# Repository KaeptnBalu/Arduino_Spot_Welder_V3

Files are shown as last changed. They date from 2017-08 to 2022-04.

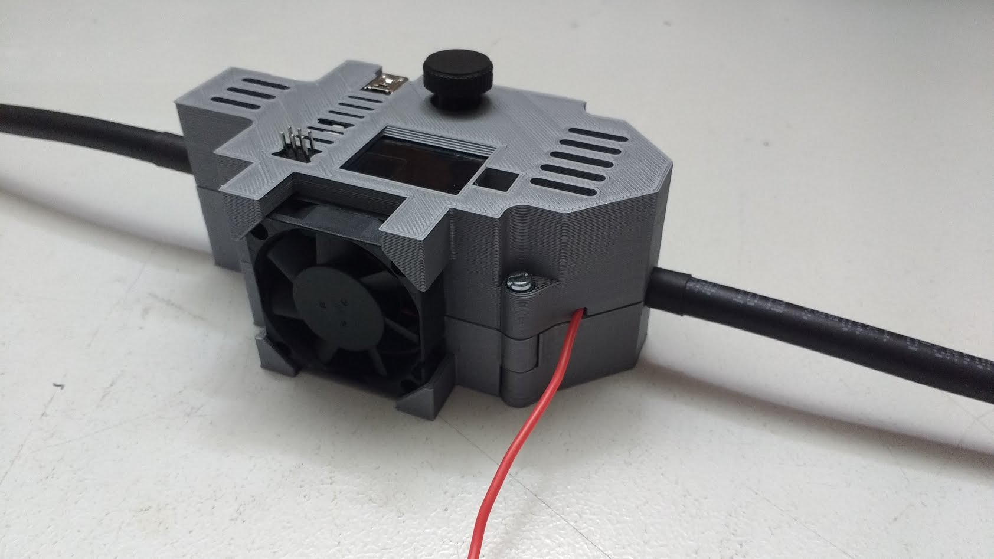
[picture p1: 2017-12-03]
Parts/Spot Welder V3 Case/SWV3_case_v2_assembly_11.jpg

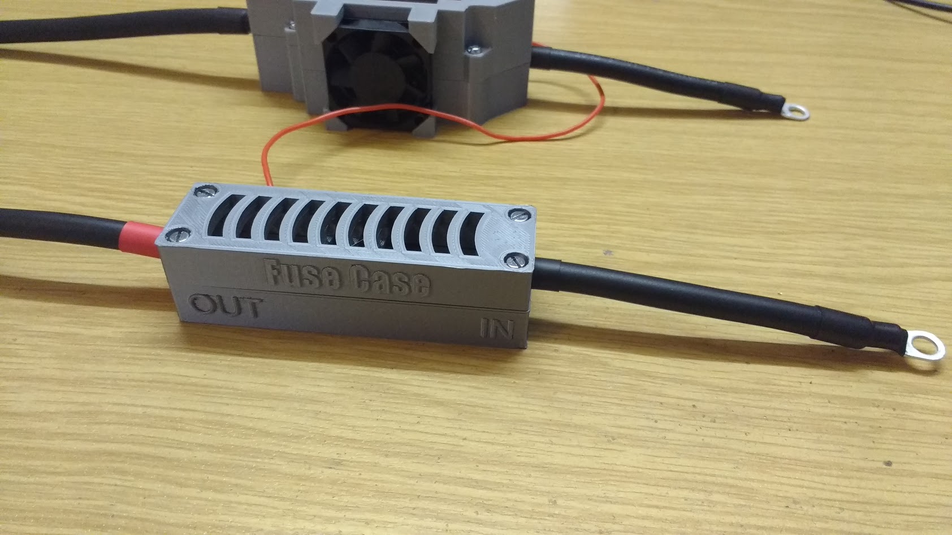
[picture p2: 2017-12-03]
Parts/Spot Welder V3 Case/Fuse_Case_assembly_14.jpg

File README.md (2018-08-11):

# Arduino_Spot_Welder_V3

This is the latest V3 of the Arduino Spot Welder. The previous V2 can be found here https://github.com/KaeptnBalu/Arduino_Spot_Welder_V2

An Arduino based Spot Welder for battery welding 
- Build Guide: http://www.instructables.com/id/DIY-Arduino-Battery-Spot-Welder/
- Introduction Video: https://www.youtube.com/watch?v=CNmvx2JSCvA
- Project Homepage: https://malectrics.eu/

Improvements in V3:

- Mosfet PCB now with 2oz copper layer and wider traces which connect the high current carrying mosfet legs to the u-shaped aluminum part
- “AutoPulse” feature, which automatically activates a pulse after a defined delay time when both welding tips touch the nickel strip (thanks to Petr Zverina for the idea)
- 7 segment display replaced by OLED display
- potentiometer replaced by rotary encoder
- Menu system to easy adjust the low battery alarm, AutoPulse delay and short pulse time
- powered directly by car battery, no more need for extra power supply
- TVS diode integrated on the mosfet pcb, no external diodes necessary
- upgraded Mosfets to IRFB7430 (they can handle up to 1000A welding current with no problem)
- Standby feature: after 5 minutes of inactivity the Spot Welder will go to standby and the foot switch and AutoPulse will be deactivated while in standby.
- u-shaped aluminum parts is now riveted to the pcb

This Spot Welder can be used to weld 18650 batteries. It uses a 12V car battery as welding current supply. Typically one 40Ah 440A battery delivers enough current to get good welds with 0.15mm nickel strips and even 0.25mm nickel strips. For thicker nickel strips maybe you will need bigger battery or two in paralell.

The Welder generates a double pulse, where the first one is 12% of the time of the second one by default. Pulse time of the main pulse is adjustable by the rotary encoder and displayed on the screen in ms so you can exactly adjust the time. Its adjustable from 1 … 100 mS by default. (adjustable up to 500ms in the system menu)

If you want to download the project click on "clone or download" on this page. Downloading single files sometimes seems to cause some files to be corrupted while downloading.

You can get parts to build your own Spot Welder or prebuilt kits at https://malectrics.eu/

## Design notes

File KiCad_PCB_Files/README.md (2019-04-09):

These are the pcb files for the Spot welder V3

V3.3
- The mosfet board was updated with following improvements: 
- Much wider traces on the bottom of the pcb for the high current connection to the u-shaped aluminum part
- Mosfet gate resistors directly on the mosfet board, very close to the mosfet gate pins
- All 8 Pins of the female 8 pin header that connects the Arduino and mosfet board are now connected to each other, which eliminates contact problems.
- compatible to all Spot Welder Arduino Boards V3 or later

V3.2
- the Arduino Board was updated so it is now possible to mount a 3.5mm terminal block to the input pads. 
- the voltage measurement now connects directly to the 12V input pad instead of behind the schottky diode in the previous version. This guarantuees a more precise voltage measurement.
- the 8 small SMAJ13A-13-F TVS diodes have been removed from the mosfet board. There is now one of these diodes on the Arduino board that protects all mosfet gates at once.

V3.1

There is a new V3.1 of the mosfet board available. It is fully compatible with the Arduino Board V3, so you only need to upgrade the mosfet board if you already built a V3 Spot Welder. 

Improvements:

    4 TVS diodes instead of only 1

This improvement makes it more capable of higher CCA rated car batteries. In my tests it handled a 800 CCA car battery for a few hundred welds in a row without problems. But using this powerfull batteries operates the welder near its maximum limits so the recommended car battery size is still 400...600 CCA

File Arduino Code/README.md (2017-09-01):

This is the Arduino Code for the Spot Welder V3. 
Do not use it with the older V2 pcbs. It is not compatible with these.

You need to have the Ardafruit_GFX library and the Ardafruit_SSD1306 library installed in your Arduino IDE to sucessfully compile the Code.

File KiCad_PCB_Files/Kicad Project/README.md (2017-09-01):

These are the KICAD project files for the Arduino Spot Welder V3

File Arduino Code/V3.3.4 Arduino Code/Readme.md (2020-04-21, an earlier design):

This is V3.3.4 of the Arduino Code

Improvements:

- fix weld counter, it can now count up to 65535
- add over volatge warning when input voltage is 14.5 V or higher

When upgrading from an earlier V3 version of the Arduino Code to this one you need to perform a full reset of the welder in the system menu after the update.

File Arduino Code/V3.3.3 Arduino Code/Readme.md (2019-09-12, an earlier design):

This is V3.3.3 of the Arduino Code

Improvements:

- fix slow progress bar drawing problem

You can also apply this fix to older versions of the Arduino Code. All you have to do is change this line of code in the drawProgress function:

        res = ++o->step > steps;

to these two lines:

        o->step = (int)(millis()-o->millis)/(o->time/steps);
        res = o->step > steps;

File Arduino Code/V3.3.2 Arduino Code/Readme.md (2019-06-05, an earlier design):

This is V3.3.2 of the Arduino Code

Improvements:
- Weld time can be set down to 1ms (before minimum was 3ms)
- Short Pulse (preheat pulse) percentage can be adjusted down to 0% (0% turns the short pulse off)
- on weld times below 3ms the short pulse (preheat pulse) will be automatically disabled
- battery voltage only updates about every 15 seconds now
- low battery message can be canceled by clicking the rotary encoder
- code is now compatible with the newer Adafruit SSD1306 and GFX library versions

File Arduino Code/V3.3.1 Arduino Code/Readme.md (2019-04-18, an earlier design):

Improvements in V3.3.1
- The Welder will now recognize if the foot switch is wired wrong and display an error message.

Description:
The foot switch needs to be used in no configuration, if it is connected in nc configuration (which means contacts closed when the switch is not pushed) an error message will be displayed during the start up of the spot welder.

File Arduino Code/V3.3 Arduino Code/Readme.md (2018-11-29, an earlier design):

Changes in V3.3

The Auto Pulse feature was improved. 
Many thanks to the Spot Welder user Arturs Jelohovskis for implementing this feature into the Arduino code.

What it does:
- added indication of probes shortcut on the screen
- added indication of delay BEFORE welding as progress bar (if probes are disconnecting during wait then AutoPulse stops)
- added indication of delay AFTER the welding pulse as progress bar.

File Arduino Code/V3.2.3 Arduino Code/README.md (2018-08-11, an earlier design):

Changes in V3.2.3

Bugfix: 
The weld counter does now automatically reset to 0 as soon as it reaches 9999 welds.
This was done because the display failed when the weld counter reached 10.000 welds, due to problems with variable types.

In case you dont want to update your software to the latest version:
In the older software versions you can solve the display problem by doing a "Full Reset" in the system menu. 
This will reset the weld counter to 0. Then you can do 9999 welds before the problem occurs again.

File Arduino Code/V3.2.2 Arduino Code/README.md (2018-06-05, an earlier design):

Changes in V3.2.2:

The software reset function has been removed because there were many complains that it is to complicated to update the Arduino Nano Bootloder. 
This change eliminates the need to install the SoftwareReset library and you also dont need to change the default bootloader of the Arduino Nano to the OptiBoot Bootloader anymore.

How does this change the Spot Welder usability ?

When you are in the sytem menu and click on the reboot, the safe reset or the full reset button you need to power of the Spot Welder manually to perform a reset.

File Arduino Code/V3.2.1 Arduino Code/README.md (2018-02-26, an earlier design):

This is version 3.2.1 of the Arduino Code.

New features:
The Version 3.2.1 Update introduces a weld pulse measurement feature.
This feature allows the Spot Welder to measure the voltage drop across the two welding cables and the Spot Welder itself. 
From that value it then calculates the Amps.

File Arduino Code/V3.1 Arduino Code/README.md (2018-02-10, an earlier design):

This is the new completely redesigned V3.1 Arduino Code for the Arduino Spot Welder.

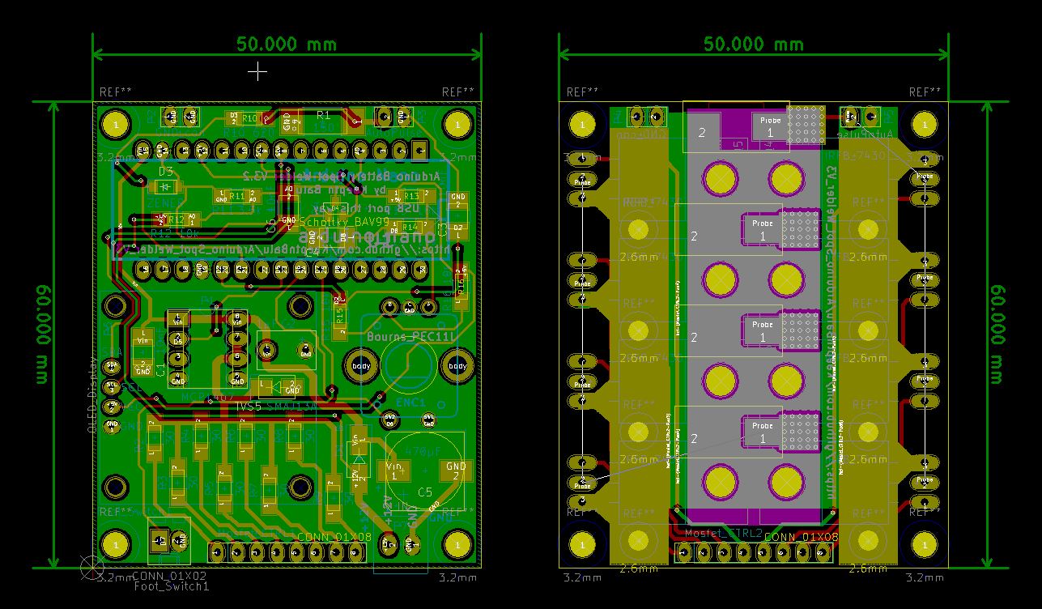
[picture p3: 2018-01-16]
KiCad_PCB_Files/Spot_Welder_V3.2_PCB_Layout.JPG

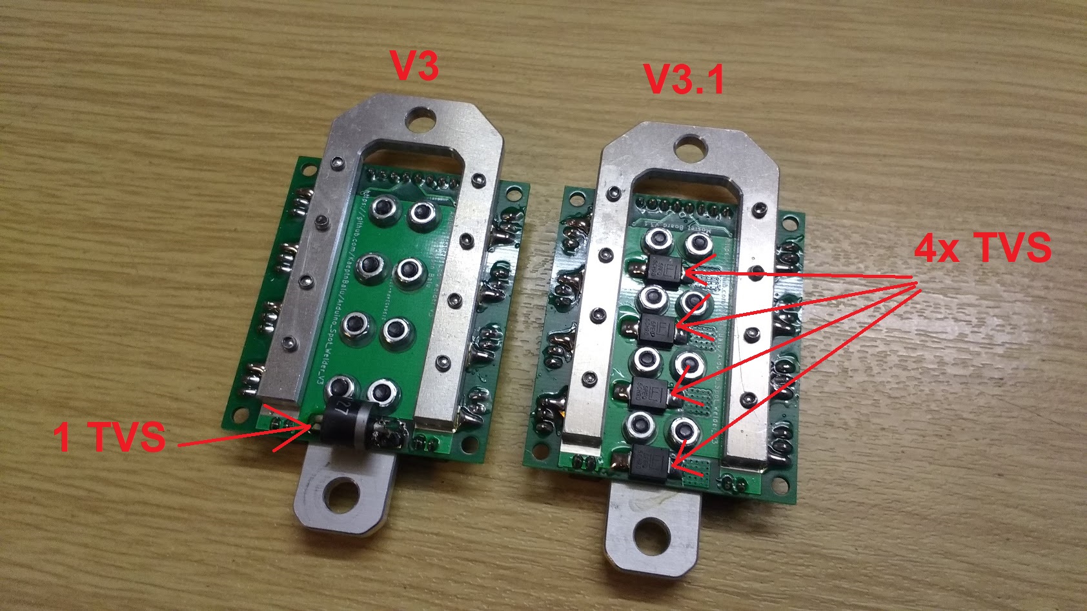
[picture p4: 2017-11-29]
KiCad_PCB_Files/mosfet_pcb_V3_vs_V3.1.jpg

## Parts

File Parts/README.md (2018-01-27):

<b>For a complete parts list take a look at the BOM file</b>

These are the parts you need to buy for building the Spot Welder V3. With the Mouser.com Shop Link you can directly ad all electronic component parts to your shopping cart. 

Not included in the Mouser shopping cart:
- 1x Arduino Nano
- 1x OLED Display

Parts I bought at the local hardware store:

- 1x piece of 16x70mm aluminium about 3 or 4mm thick
- Some 16mm² cable and short piece of thick solid copper wire for the probes tips

You can get ready made welding cables, aluminum parts and pcb sets at www.malectrics.eu if you dont want to make them yourself.

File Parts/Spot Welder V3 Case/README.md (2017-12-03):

This is a 3d printable case for the Arduino Spot Welder V3.

The files are available to download from thingiverse:

https://www.thingiverse.com/thing:2600227

https://www.thingiverse.com/thing:2615364

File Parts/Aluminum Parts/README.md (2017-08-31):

Use the PDF template to cut the aluminum pieces from 4mm material.

The u-shaped piece is optional. You can either solder the thick wire bend to an u-shape directly to the pcb as before or cut this aluminum piece and screw it with m2 screws to the pcb.

You can also take a look at the 3d and dxf drawings to manufacture the aluminum parts with a cnc or something else.

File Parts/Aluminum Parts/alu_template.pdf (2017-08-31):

# Cut from 3 - 4 mm thick aluminum

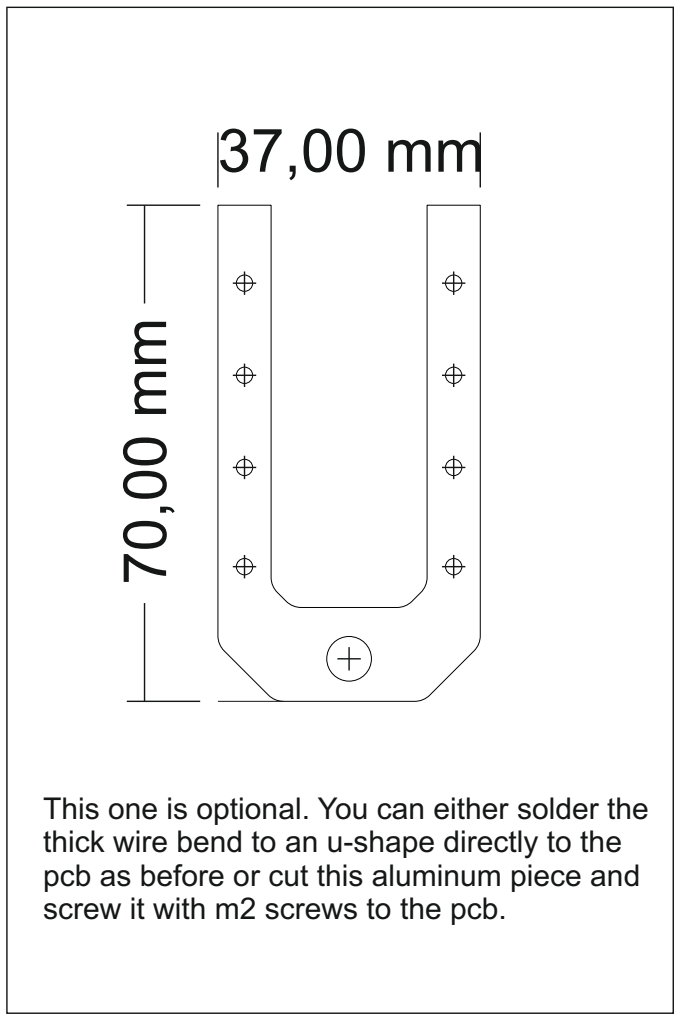
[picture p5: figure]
screw it with m2 screws to the pcb.

This one is optional. You can either solder the thick wire bend to an u-shape directly to the pcb as before or cut this aluminum piece and

70,00 mm

17,00 mm

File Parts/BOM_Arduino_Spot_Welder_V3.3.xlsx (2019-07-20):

 |  | Mouser.com Parts |  | Complete Shopping Card Link (https://www.mouser.com/ProjectManager/ProjectDetail.aspx?AccessID=131d2ccc2d)
Quantity | PCB Reference | Name | Mouser.com Part Number | Price/piece | Price all | Note
8 | IRFB_7430 | Mosfet IRFB 7430 40V 409A | 942-IRFB7430PBF (http://www.mouser.de/Search/ProductDetail.aspx) | 2.76 € | 22.08 €
1 | P1 MCP1407 | Mosfet Driver MCP1407-E/P | 579-MCP1407-E/P (http://www.mouser.de/Search/ProductDetail.aspx) |  | 0.90 €
1 | Bourns_PEC11L | Rotary Encoder | 652-PEC11L4220FS0015 (http://www.mouser.de/Search/ProductDetail.aspx) |  | 1.70 €
2 | Arduino Nano | 1x15 Pol Female Pin Header | 992-15FX1-254MM (http://www.mouser.de/Search/ProductDetail.aspx) | 1.06 | 2.12 €
1 | Mosfet_CTRL2 | 1x8pol female header | 437-8018700810001101 (http://www.mouser.de/Search/ProductDetail.aspx) | 0.66 € | 0.81 €
2 | P4,P5 | 1x2pol female header | 437-8018700210001101 (http://www.mouser.de/Search/ProductDetail.aspx) | 0.221 | 0.44 €
1 | OLED_Display | 1x4pol female header | 517-974-01-04-RK (http://www.mouser.de/Search/ProductDetail.aspx) |  | 0.62 €
1 | Mosfet_CTRL1, P2, P3 | 1x16 Pol Male Pin Header | 538-22-28-4160 (http://www.mouser.de/Search/ProductDetail.aspx) |  | 0.66 €
1 | Foot_Switch | PCB connector 2pin | 710-61900211121 (http://www.mouser.de/Search/ProductDetail.aspx) |  | 0.48 €
1 | P7 | Terminal Block | 710-691214110002 (https://www.mouser.de/ProductDetail/710-691214110002) |  | 0.75 €
1 | P1 MCP1407 | IC socket 8 pole | 571-1-2199298-2 (http://www.mouser.de/Search/ProductDetail.aspx) |  | 0.09 €
1 | D1 | SMD-Schottky 60V 1A | 750-CDBA160-G (http://www.mouser.de/Search/ProductDetail.aspx?R=CDBA160-Gvirtualkey59960000virtualkey750-CDBA160-G) |  | 0.34 €
1 | Zener D3 | SMD Zener diode 4,3V 0,5W | 78-MMSZ4687-E3-08 (http://www.mouser.de/Search/ProductDetail.aspx) |  | 0.17 €
1 | D4 | Schottky BAV99 | 863-BAV99LT1G (http://www.mouser.de/Search/ProductDetail.aspx?R=BAV99LT1Gvirtualkey58410000virtualkey863-BAV99LT1G) |  | 0.10 €
4 | TVS | TVS Diode 14,4V 5kW | 576-5.0SMDJ13A (https://www.mouser.de/ProductDetail/576-5.0SMDJ13A) | 1.69 € | 6.76 €
1 | TVS5 | TVS Diode 13V 400W | 621-SMAJ13A-13-F (http://www.mouser.de/Search/ProductDetail.aspx) |  | 0.32 €
1 | C2 | film capacitor 1 µF RM5 | 505-MKS2C041001FMSSD (http://www.mouser.de/Search/ProductDetail.aspx) |  | 0.26 €
4 | C1, C3, C4, C6 | ceramic capacitor 0,01µF SMD | 581-12103D103MAT2A (http://www.mouser.de/Search/ProductDetail.aspx) | 0.17 € | 0.51 €
1 | C5 | electrolytic capacitor 470µF 25V | 647-UWT1E471MNL1S (http://www.mouser.de/Search/ProductDetail.aspx) |  | 0.52 €
1 | R1 | Resistor 1206 SMD 1 kOhm | 603-AC1206FR-071KL (https://www.mouser.de/ProductDetail/Yageo/AC1206FR-071KL?qs=sGAEpiMZZMu61qfTUdNhG19HzxXL1i6itFKVZ7nWm2k%3D) |  | 0.10 €
10 | R2, R3, R4, R5, R6, R7, R8, R9 | Resistor 1206 SMD 30 Ohm | 603-RC1206FR-0730RL (http://www.mouser.de/Search/ProductDetail.aspx) | 0.02 | 0.20 €
10 | R17,R18,R19,R20,R21,R22,R23,R24 | Resistor 1206 SMD 30 Ohm | 603-RC1206FR-0730RL (http://www.mouser.de/Search/ProductDetail.aspx) | 0.02 | 0.20 € | optional to make the Arduino Board compatible with mosfet boards older than V3.3. If you only use V3.3 mosfet boards you can bridge the pads instead of populating resistors.
10 | R10 | Resistor 1206 SMD 620 Ohm | 603-RC1206FR-07620RL (http://www.mouser.de/Search/ProductDetail.aspx) | 0.02 € | 0.20 €
10 | R11 | Resistor 1206 SMD 3,3 kOhm | 603-RC1206FR-073K3L (http://www.mouser.de/Search/ProductDetail.aspx) | 0.02 € | 0.20 €
10 | R12 … R16 | Resistor 1206 SMD 10 kOhm | 603-RC1206FR-0710KL (http://www.mouser.de/Search/ProductDetail.aspx) | 0.02 € | 0.20 €
 |  |  | Components Total: |  | 40.73 €
 |  |  | incl. 19%tax |  | 48.47 €
 |  |  | Other Parts
Quantity |  | Name | Description | Price/piece | Price all | Link / Where to buy
1 |  | Arduino Nano |  |  | 2.15 € | https://www.banggood.com/ATmega328P-Nano-V3-Controller-Board-Compatible-Arduino-p-940937.html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
1 |  | OLED Diplay 0,96" 128x64 | take care of correct pinout (GND - VCC - SCL - SDA) |  | 4.73 € | https://www.banggood.com/0_96-Inch-12864-OLED-Module-4-Pin-IC-I2C-IIC-Communication-p-1219948.html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
1 |  | Alu 17x70x4mm + 37x70x4mm | see alu_template.pdf (https://github.com/KaeptnBalu/Arduino_Spot_Welder_V2/blob/master/Parts/Aluminum_Parts/alu_template.pdf) |  | 2 € | local hardware Store or https://malectrics.eu/
8 |  | M3x10 screw + nuts | for mosfets assembly |  | 0.50 € | local hardware store
8 |  | M3 Nylon Washers | for mosfets assembly |  | 0.50 € | local hardware store
8 |  | M2.5x8 screws + nuts | for u-alu ssembly |  | 0.50 € | local hardware store
1 |  | 1m 16 mm² flexible cable | for welding cable |  | 3 € | e.g. old car starter cable or https://www.schweisshelden.de/schweisskabel-h01n2-d-16-mm2-48129
1 |  | 0,1m 16mm² solid copper wire | for the welding tips |  | 1 € | local hardware store
2 |  | cable lug for 16 mm² | for welding cable | 0.6 | 1.20 € | local hardware store or http://www.voelkner.de/products/9287/Ringkabelschuh-16-25mm-6mm-Gelb.html
1 |  | Luster Terminal 16mm² | welding tip connection |  | 2.00 € | local hardware store
1 |  | battery terminals | for car battery |  | 2.95 € | local hardware store or https://malectrics.eu/
1 |  | PCB Set | Arduino + Mosfet PCB |  | 5.95 € | https://malectrics.eu/
2 |  | nylon spacers M2 x 12mm + M2x5 screws for OLED display | OPTIONAL |  | 3.00 € | Ebay or Aliexpress
1 |  | Foot Switch | OPTIONAL |  | 5.95 € | https://malectrics.eu/
1 |  | 300A Fuse | OPTIONAL |  | 2.95 € | https://malectrics.eu/
 |  |  | Other Parts Total: |  | 38.38 €
 |  |  | TOTAL COST |  | 86.85 € | (with Optonal Parts)
 |  |  |  |  | 74.95 € | (without OPTIONAL Parts)

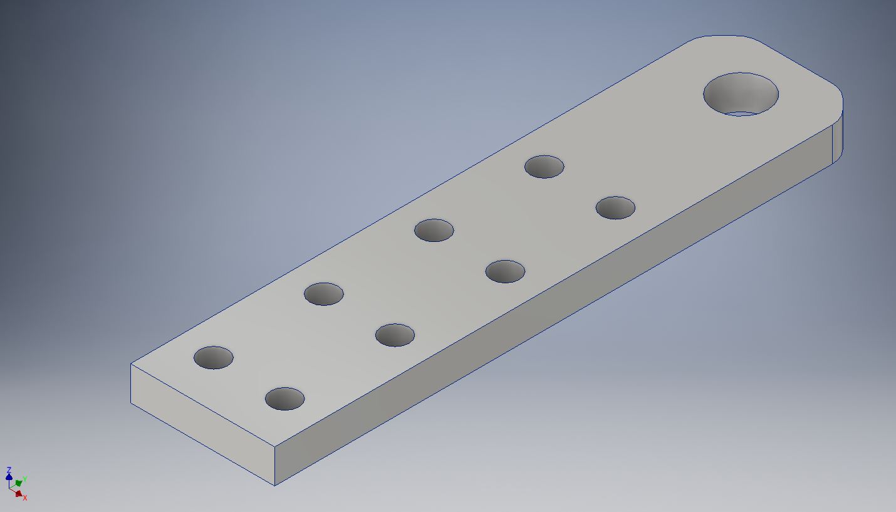
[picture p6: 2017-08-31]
Parts/Aluminum Parts/Part2_new.JPG

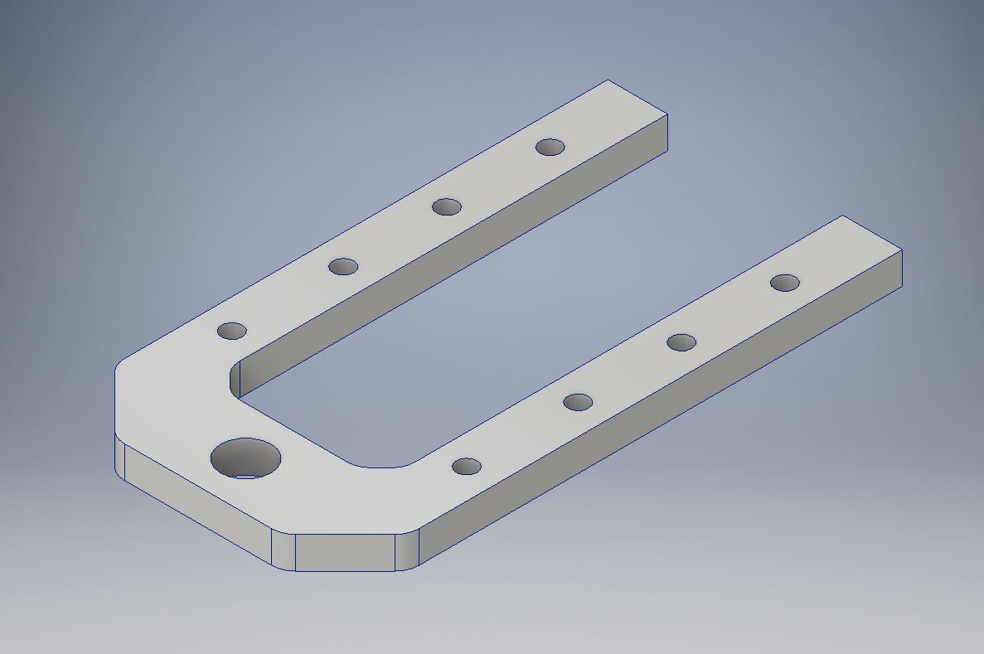
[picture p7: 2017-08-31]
Parts/Aluminum Parts/Part1_new.JPG

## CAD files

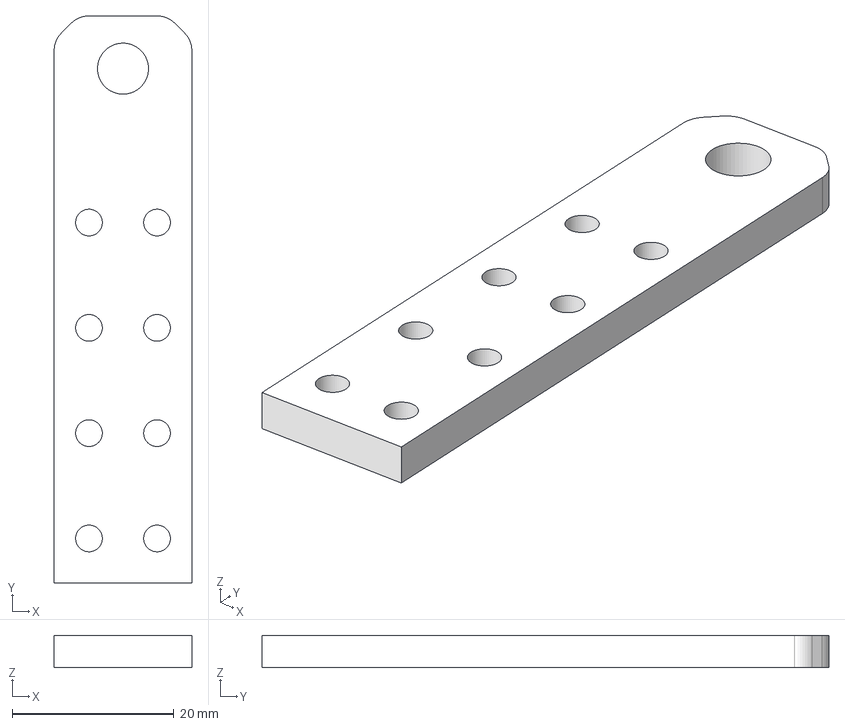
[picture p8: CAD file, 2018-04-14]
Parts/Aluminum Parts/Part2_new.stp
17.0 x 70.0 x 4.00 mm

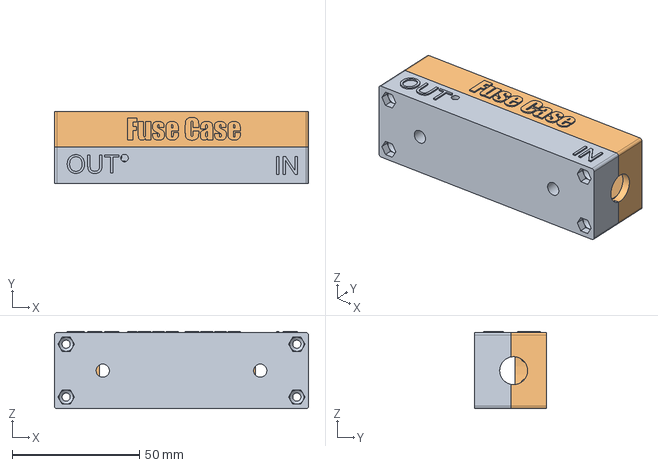
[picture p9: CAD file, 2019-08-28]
Parts/Spot Welder V3 Case/CAD Files/ANL_Fuse_Case.step
100.0 x 28.5 x 30.5 mm

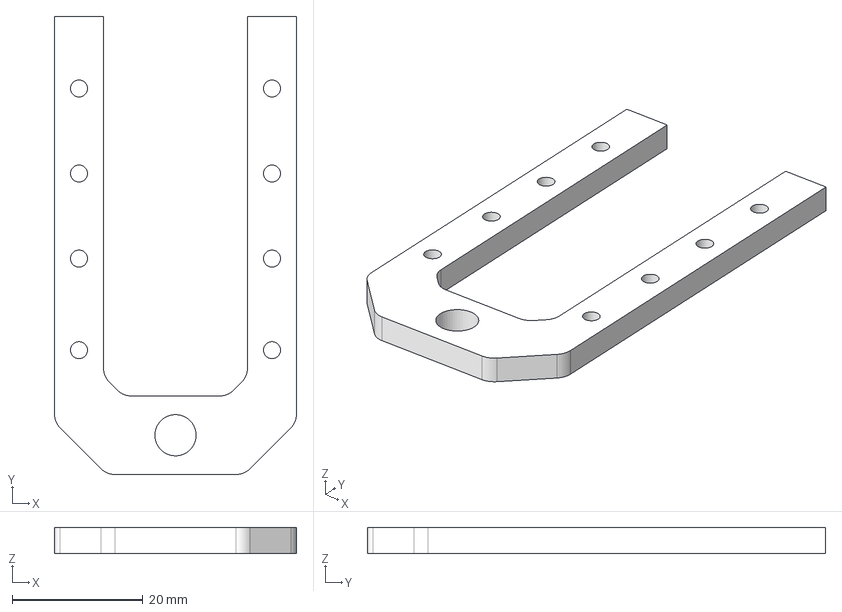
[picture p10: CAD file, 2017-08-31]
Parts/Aluminum Parts/Part1_new.stp
37.0 x 70.0 x 4.00 mm

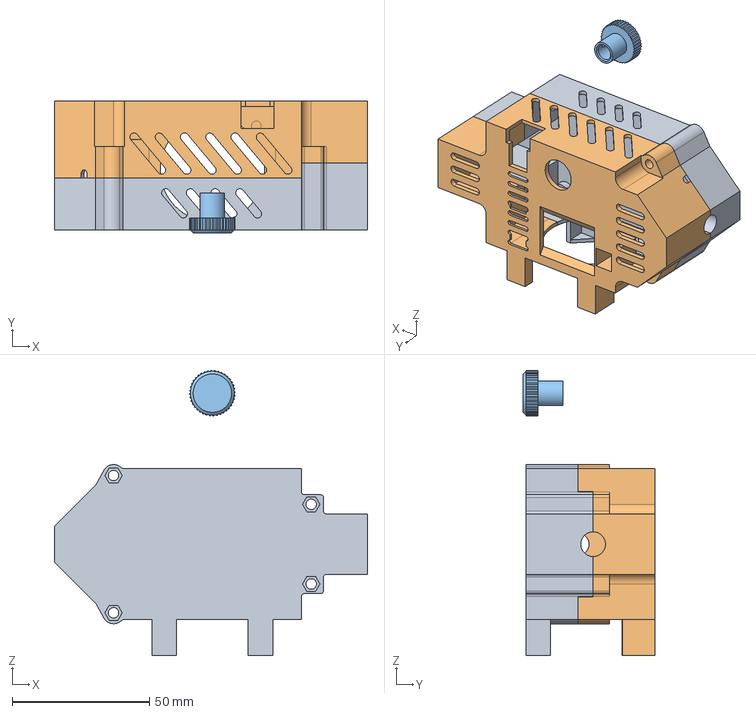
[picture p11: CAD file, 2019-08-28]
Parts/Spot Welder V3 Case/CAD Files/Case_Spot Welder_V3.step
114.0 x 48.0 x 103.9 mm

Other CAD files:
Parts/Aluminum Parts/Part1_new.dwg
Parts/Aluminum Parts/Part1_new.dxf
Parts/Aluminum Parts/Part1_new.ipt
Parts/Aluminum Parts/Part2_new.dwg
Parts/Aluminum Parts/Part2_new.dxf
Parts/Aluminum Parts/Part2_new.ipt
Parts/Spot Welder V3 Case/CAD Files/ANL_Fuse_Case.f3d
Parts/Spot Welder V3 Case/CAD Files/Case_Car_Bat_Mount_Spot Welder_V3.f3d
Parts/Spot Welder V3 Case/CAD Files/Case_Spot Welder_V3.f3d

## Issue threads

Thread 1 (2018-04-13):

Add Part2_new.stp

PaoloElMarinelo, 2018-04-13:
Hi !
First I want to say thank you for all you make in this project, it's the best spot welder I know !
Please could you add the .STP file from Part2_new in Arduino_Spot_Welder_V3/Parts/Aluminum Parts/ ?
Thank you very much.
Paolo

KaeptnBalu, 2018-04-14:
Hi,
Thanks for pointing out the missing file. I added it.

Closed 2018-04-14.

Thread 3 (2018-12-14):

V3.2.3: deprecated OLED constructor makes pin 4 unusable

crteensy, 2018-12-14:
I designed a custom top PCB with an arduino pro mini, and used pin 4 for one of the encoder inputs. That didn't work out of the box, because pin 4 appeared to be stuck high. It's not used in the schematic and also not defined in the header block with pin numbers. This was hard to track down, but:

The constructor used for the OLED display is deprecated (as per adafruit's documentation). It uses a reset pin, and the reset pin is defined as pin 4 in the OLED part of the spot welder header file (you don't have the bare source file in the repo so I can't link to it).

The correct constructor to use is (line
`Adafruit_SSD1306 display(128, 64, &Wire);       /**< OLED display object */`

And the reset pin definition can be removed:
//#define OLED_RESET          4               /**< OLED mode */

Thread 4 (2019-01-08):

Slow screen refresh rate

ignasurba, 2019-01-08:
With the latest [Adafruit_SSD1306](https://github.com/adafruit/Adafruit_SSD1306/releases/tag/1.2.9) library the I2C clock is ~32kHz, due to wireClk in the library being 0.

The following will fix the issue.
`Adafruit_SSD1306 display(OLED_RESET);       /**< OLED display object */`
change to:
`Adafruit_SSD1306 display(128, 64, &Wire, OLED_RESET, 800000L); /**< OLED display object */`

Good luck!

bseishen, 2019-04-15:
+1 on this. Redraw times at slow data rate is causing auto pulse to be nowhere accurate. 2sec is more like 10 seconds.

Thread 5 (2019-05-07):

mosfet board state led (new idea)

dreamstruct, 2019-05-07:
HI KaeptnBalu

I have an idea

About add state led to mosfet borad

Is it possible to connect the 10k resistor to the

 MCP1407 output pin and then connect the LED to GND?
This can quickly get the output state of the mosfet board

Does this cause mosfet to crash?

Please evaluate his possibilities

Thank you very much.

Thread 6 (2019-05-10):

KICAD R1 resistor in version 3.3 should be modified to 1Kom ?

dreamstruct, 2019-05-10:
I see in other version is for 150 ohm resistor SMD 3521 2w
However, version 3.3 was changed to 1206 1kom
Is this a bug?

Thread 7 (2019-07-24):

Version 3.3

snmcma, 2019-07-24:
Version 3.3 in a working state, or is it only a temporary project? Can I order a fee from Chinese friends?

KaeptnBalu, 2019-07-24:
Version 3.3 is working fine

snmcma, 2019-08-31:
>
>
> Version 3.3 is working fine

what could be the problem? in version 3.3.2 the display does not work, in version 3.3.1 the display works fine. Where could there be a mistake?

KaeptnBalu, 2019-09-01:
V3.3.2 reqires a new library versions for the display.
(Adafruit SSD1306 V1.2.9 and Adafruit GFX V1.5.3)
For more details see https://malectrics.eu/2019/06/05/arduino-spot-welder-software-installing-tutorial-v3-3-2/

snmcma, 2019-09-01:
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

nice! thnks!

snmcma, 2019-11-03:
I used another encoder (which was at hand, I always go all the way to one side (minus) it doesn’t matter which way I turn the encoder. (there is a flaw in the library)
after assembly, my welding worked 1 time and didn’t work anymore (something went wrong). In automatic mode, should there be voltage across the contacts of the electrodes? (I think one of the mosfets struck me, it shows a voltage slightly less than the input)

snmcma, 2019-11-03:
Is it not difficult for you to take large photographs from all sides? I want to make sure the assembly is correct.

KaeptnBalu, 2019-11-03:
Hi,
Did you take a look at the assembly instructions: https://malectrics.eu/pcb-set-v3-3-assembly-instructions/
There are a lot of pictures, so you can check if you got everything correct.

Measuring the battery voltage at the welding tips is normal. If it instantly sparks when you touch the nickel, then there is a problem somewhere.

snmcma, 2019-11-03:
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
he writes the data of the current pulse, but there was no pulse on the electrodes. after each pulse, you need to click on the encoder so that I can try again to make a pulse, is this normal behavior?

snmcma, 2019-11-03:
This is not too much current I had on the pulse, mosfets could burn out? I used a powerful 160,000 microfarad capacitor in parallel with the power.

snmcma, 2020-05-17:
Can you give an answer what is the reason? It works on a small power supply, but when I connect it to a car battery, I don’t learn to weld. firmware updated to 3.3.4

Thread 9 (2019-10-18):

Display Issue

Courty40, 2019-10-18:
FYI - Had an odd problem yesterday, couldn't get the OLED display to work, tried the correct libs and scanned the i2c port (I could see the display on 0x3C).

In the end I had to do the following to get it to initialise

//Adafruit_SSD1306 display(128, 64, &Wire, OLED_RESET, 800000L); /**< OLED display object */
Adafruit_SSD1306 display(OLED_RESET);

Display is a standard Chinese OLED one with the correct pin outs, described as a "SSD1306 AA140"

If I get a min will look further but all seems to be working OK..

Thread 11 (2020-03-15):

V3.3.3 Arduino Code selectedSubMenu not assigned value correctly

richard-scott, 2020-03-15:
I've migrated your code over to using PlatformIO, and I get this error when compiling it:

> Arduino Spot Welder/src/Arduino_Spot_Welder_V3_3_3.ino:539:37: warning: statement has no effect [-Wunused-value]
>                      selectedSubMenu == 0;

It is from this section:
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

My repo is here:
https://github.com/richard-scott/Arduino_Spot_Welder_V3

richard-scott, 2020-04-01:
I've squashed the error in my repo here:
https://github.com/richard-scott/Arduino_Spot_Welder_V3
I'll create a PR.

KaeptnBalu, 2020-04-01:
Awesome Job Richard. Thank you so much for your work. This actually fixed the 10.000 welds counter bug. It can now count above 10.000 without creating an error. I will implement your fix in a new V3.3.4 of the spot welder software.

Closed 2020-04-01.

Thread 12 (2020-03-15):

V3.3.3 Arduino Code - integer implicitly truncated to unsigned type

richard-scott, 2020-03-15:
I'm getting this error when compling code:

```
Arduino_Spot_Welder_V3_3_3.ino:1076:74: warning: large integer implicitly truncated to unsigned type [-Woverflow]
     setTextProp(1, (SSD1306_LCDWIDTH-(sizeof(LS_PULSEV)-1)*CHR_W*2)/2, 16);
                                                                          ^
```
This is the section of code:
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

I've not yet got a fix for it.

richard-scott, 2020-04-01:
I've squashed the error in my repo here:
https://github.com/richard-scott/Arduino_Spot_Welder_V3
I'll create a PR.

Closed 2020-04-01.

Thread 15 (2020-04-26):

Blown legs to fets

plsommerton, 2020-04-26:
Hi. This welder v3 used for only third time today decided to blow several of the fet layer legs. Any ideas what may be causing it? Cheers.phil

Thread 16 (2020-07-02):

nothing happens when button is pressed

stefi01, 2020-07-02:
the screen works ok and the pot when turned left or right moves up and down through the milliseconds but when pressed to select or set nothing happens, am i missing something, checking the arduino sketch does not reveal any pin numbers so i am a bit lost, this is a home build and not a kit, pcb is ok and was made by jlbpcb.

KaeptnBalu, 2020-07-03:
The button of the encoder is connected to GNG and pin D6 on the Arduino Nano. When you push it Pin D6 should be pulled to GND.

stefi01, 2020-07-03:
found it, got it working, thanks :)

Closed 2020-07-03.

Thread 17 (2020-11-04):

Weld current estimate to check for propper weld

geo99918, 2020-11-04:
I saw that the weld current is estimated based on the source voltage during the weld pulse, why not use this estimation as a check for a proper weld and trigger an alarm when the current was too low, or even add a menu to set the min and max values for weld current.
E.g. with a discharged car battery 12V is present at idle but during the weld pulse the voltage drops to less than 3 volts and a good weld is not created.
A more advanced version of this would be to measure the total energy delivered to the weld but this might be for another day.

Regards,
George

KaeptnBalu, 2020-11-05:
A llittle problem with the weld current measurement is that it is not super accurate. The welder uses a fixed resistance value to calculate the current flow. It can not measure the resistance itself, just the voltage drop during the pulse. This resistance can change quite a bit depending how the welding tips are placed on the nickel and how good the contact of the wleding cables is.

I think the idea to set a weld current alarm is pretty good. For that the current measurement should be accurate enough.

To calculate the total energy during pulse and then base the pulse length on that, the current measurement needs to be more precise.  If you got an idea how the welder could do a precise resistance measurement (without complicated hardware) before a weld, that would be great. I think an option to choose between energy based welding and fixed time welding would be preatty cool.

geo99918, 2020-11-05:
Maybe the current can be measured by measuring the voltage drop across a big shunt.
if current and voltage are known during the weld event a better estimation can be done if the weld was successful or not.
Maybe the resistance can be estimated using V and I but the power source internal resistance can't be ignored in this calculation.
Regarding the alarm, a buzzer would be nice to indicate that something went wrong, usually when welding the eyes are on the weld not on the screen.

Satys27, 2025-02-05:
Ok wait for my Project release, I have improved lots of features like robotic arm will weld you just need to seat tight infront of it.

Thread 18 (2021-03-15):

v3.3.4 freeze

corbolais, 2021-03-15:
Hi,
Thanks for this project, I love it.

When doing a couple of welds, the arduino regularly freezes. Only way to continue is a reset.

Any ideas as to why it is happening or what might cause it?

It happens with standard settings and modified settings as well.

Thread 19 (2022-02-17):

CAD Files

Thegribbs, 2022-02-17:
The CAD files for the design on Thingiverse (https://www.thingiverse.com/thing:2600227/files) are designed with a cutout for the battery terminal.
Do you have a copy of the f3d file for that design?

KaeptnBalu, 2022-02-19:
The f3d file has been added

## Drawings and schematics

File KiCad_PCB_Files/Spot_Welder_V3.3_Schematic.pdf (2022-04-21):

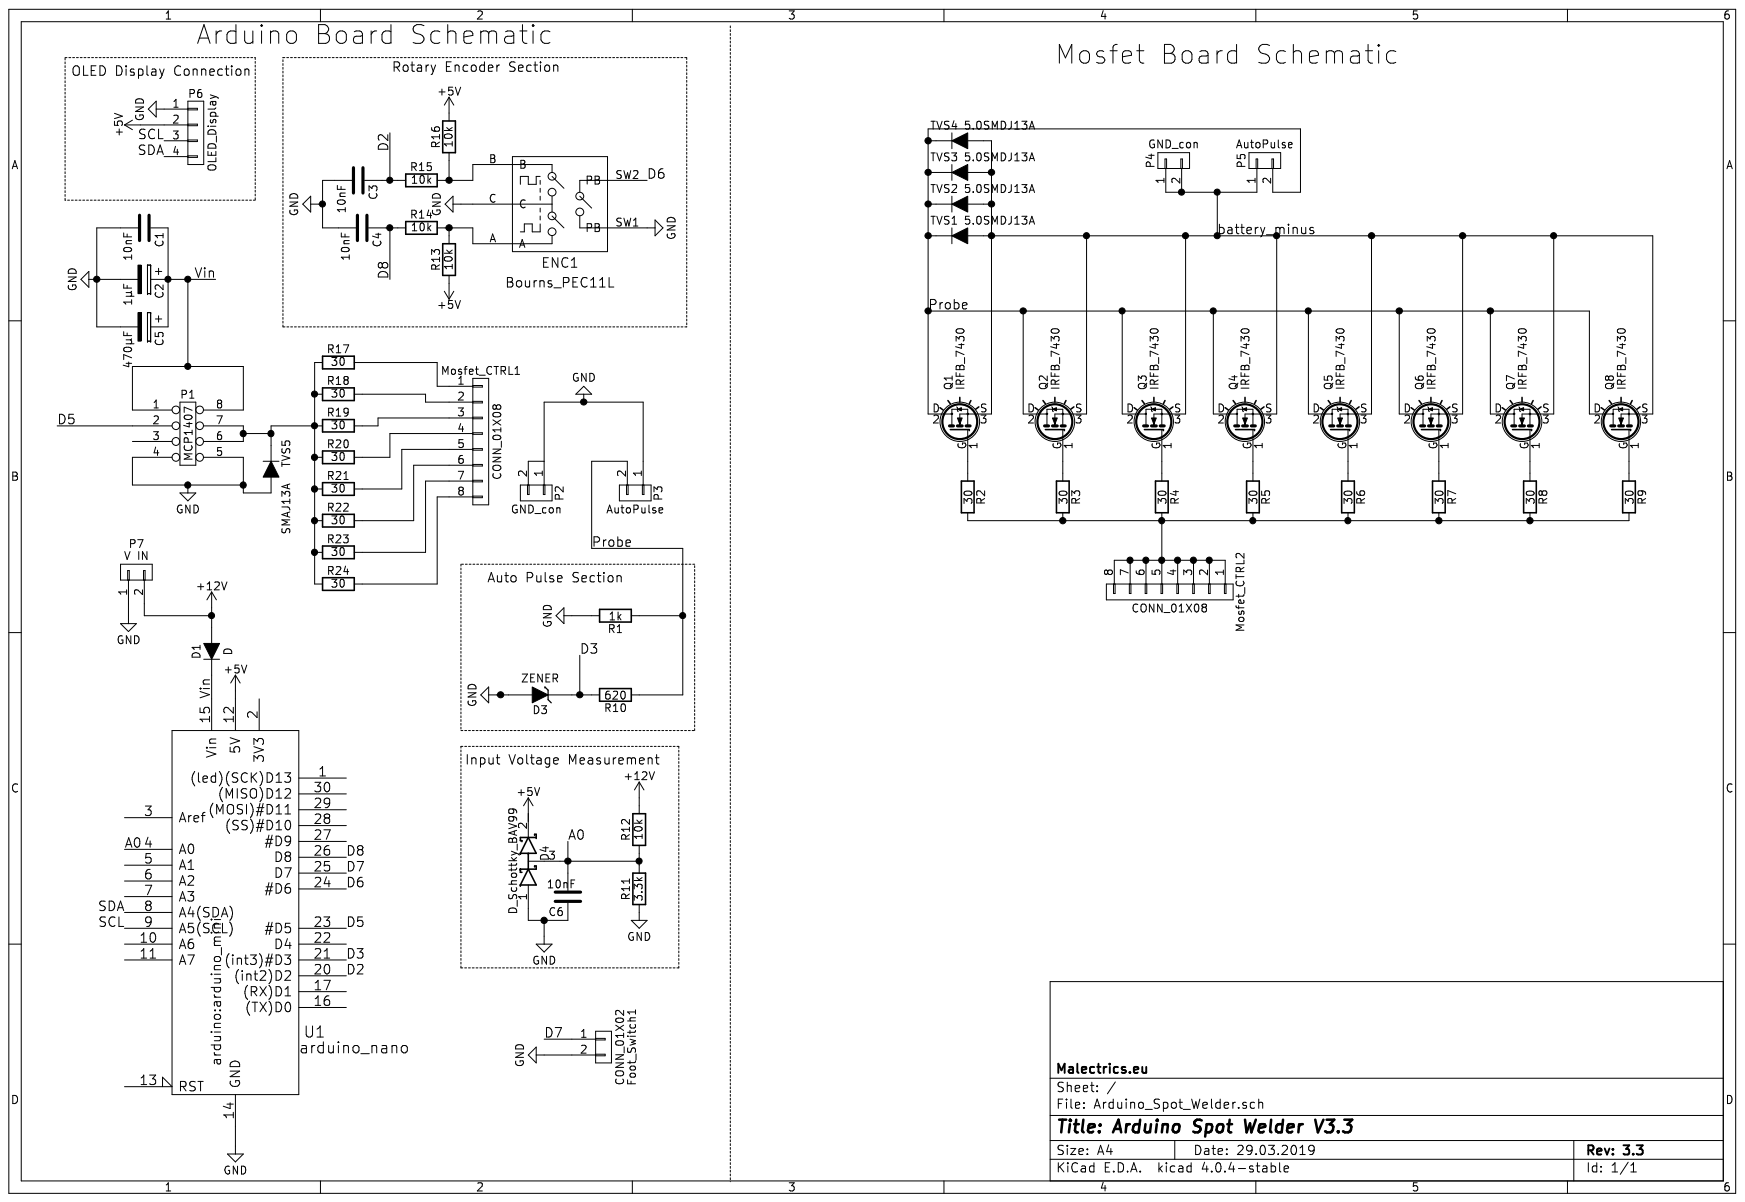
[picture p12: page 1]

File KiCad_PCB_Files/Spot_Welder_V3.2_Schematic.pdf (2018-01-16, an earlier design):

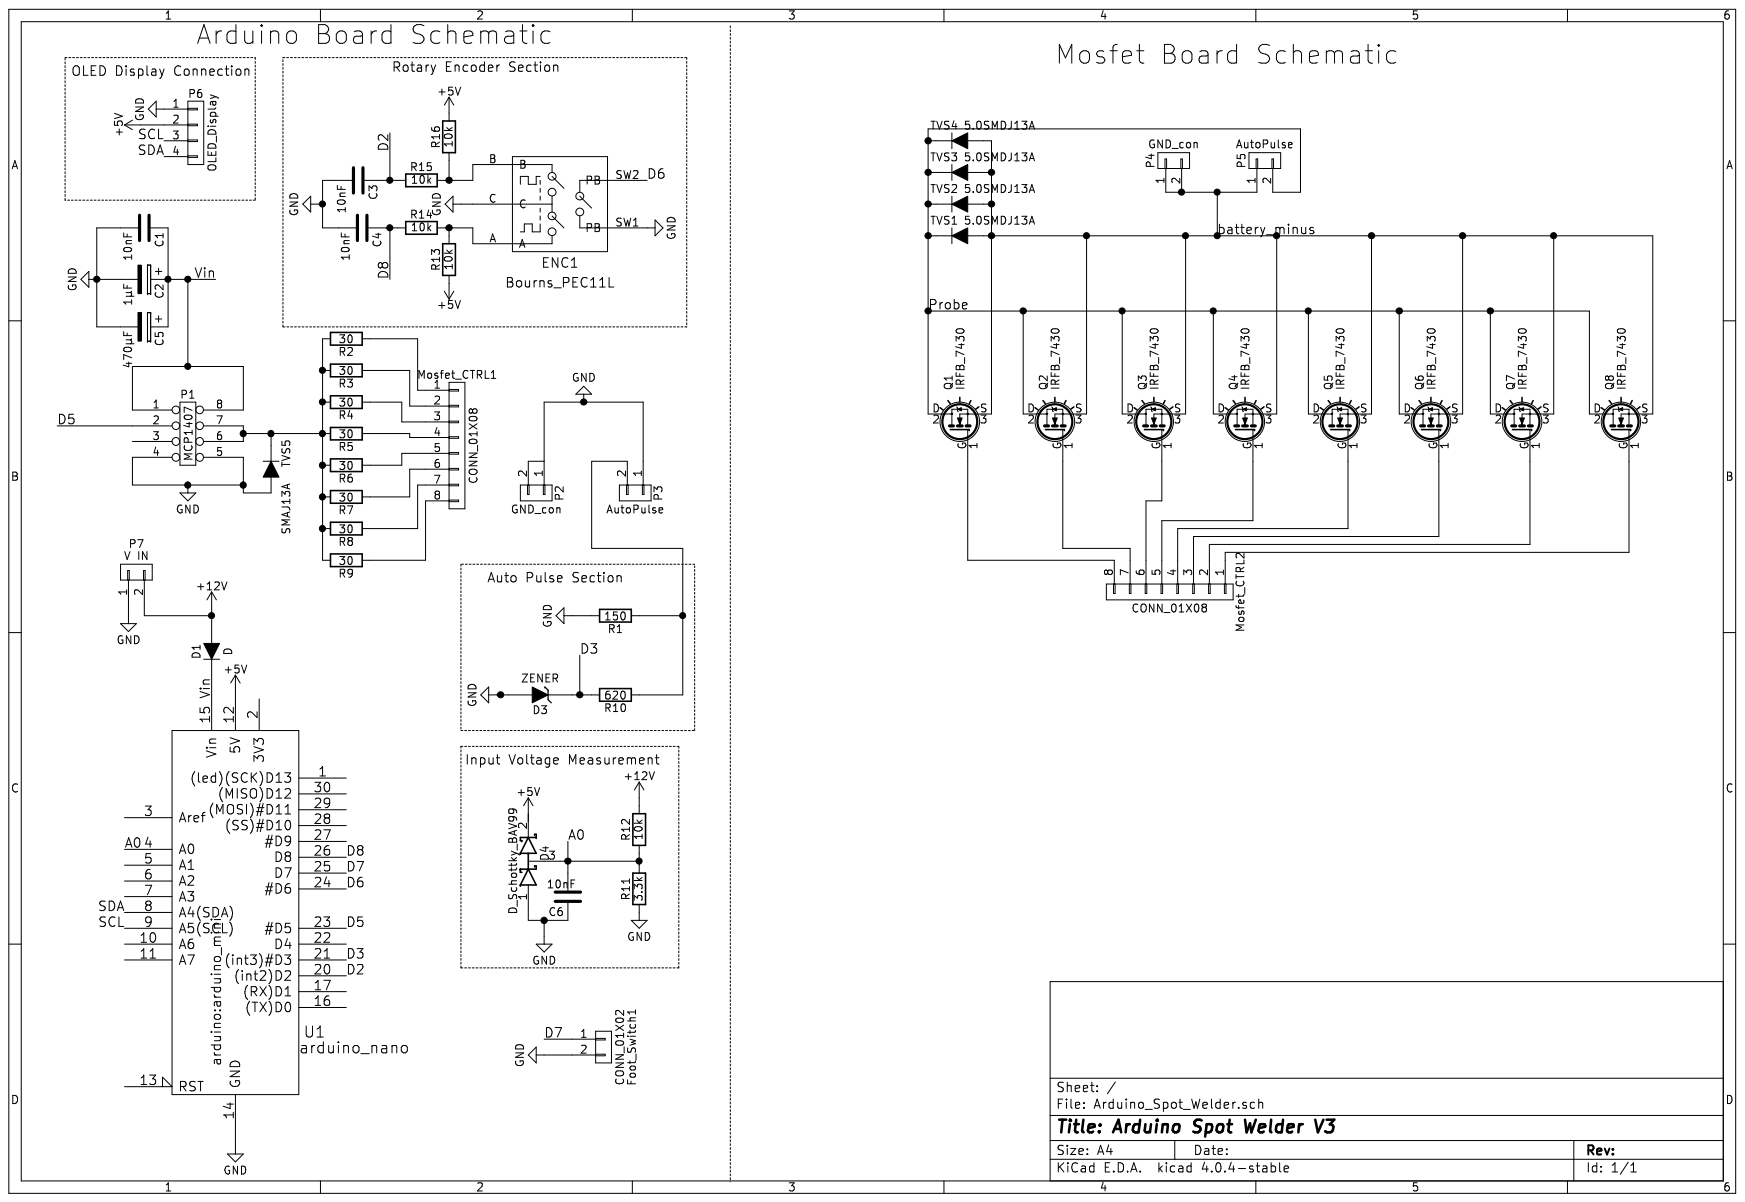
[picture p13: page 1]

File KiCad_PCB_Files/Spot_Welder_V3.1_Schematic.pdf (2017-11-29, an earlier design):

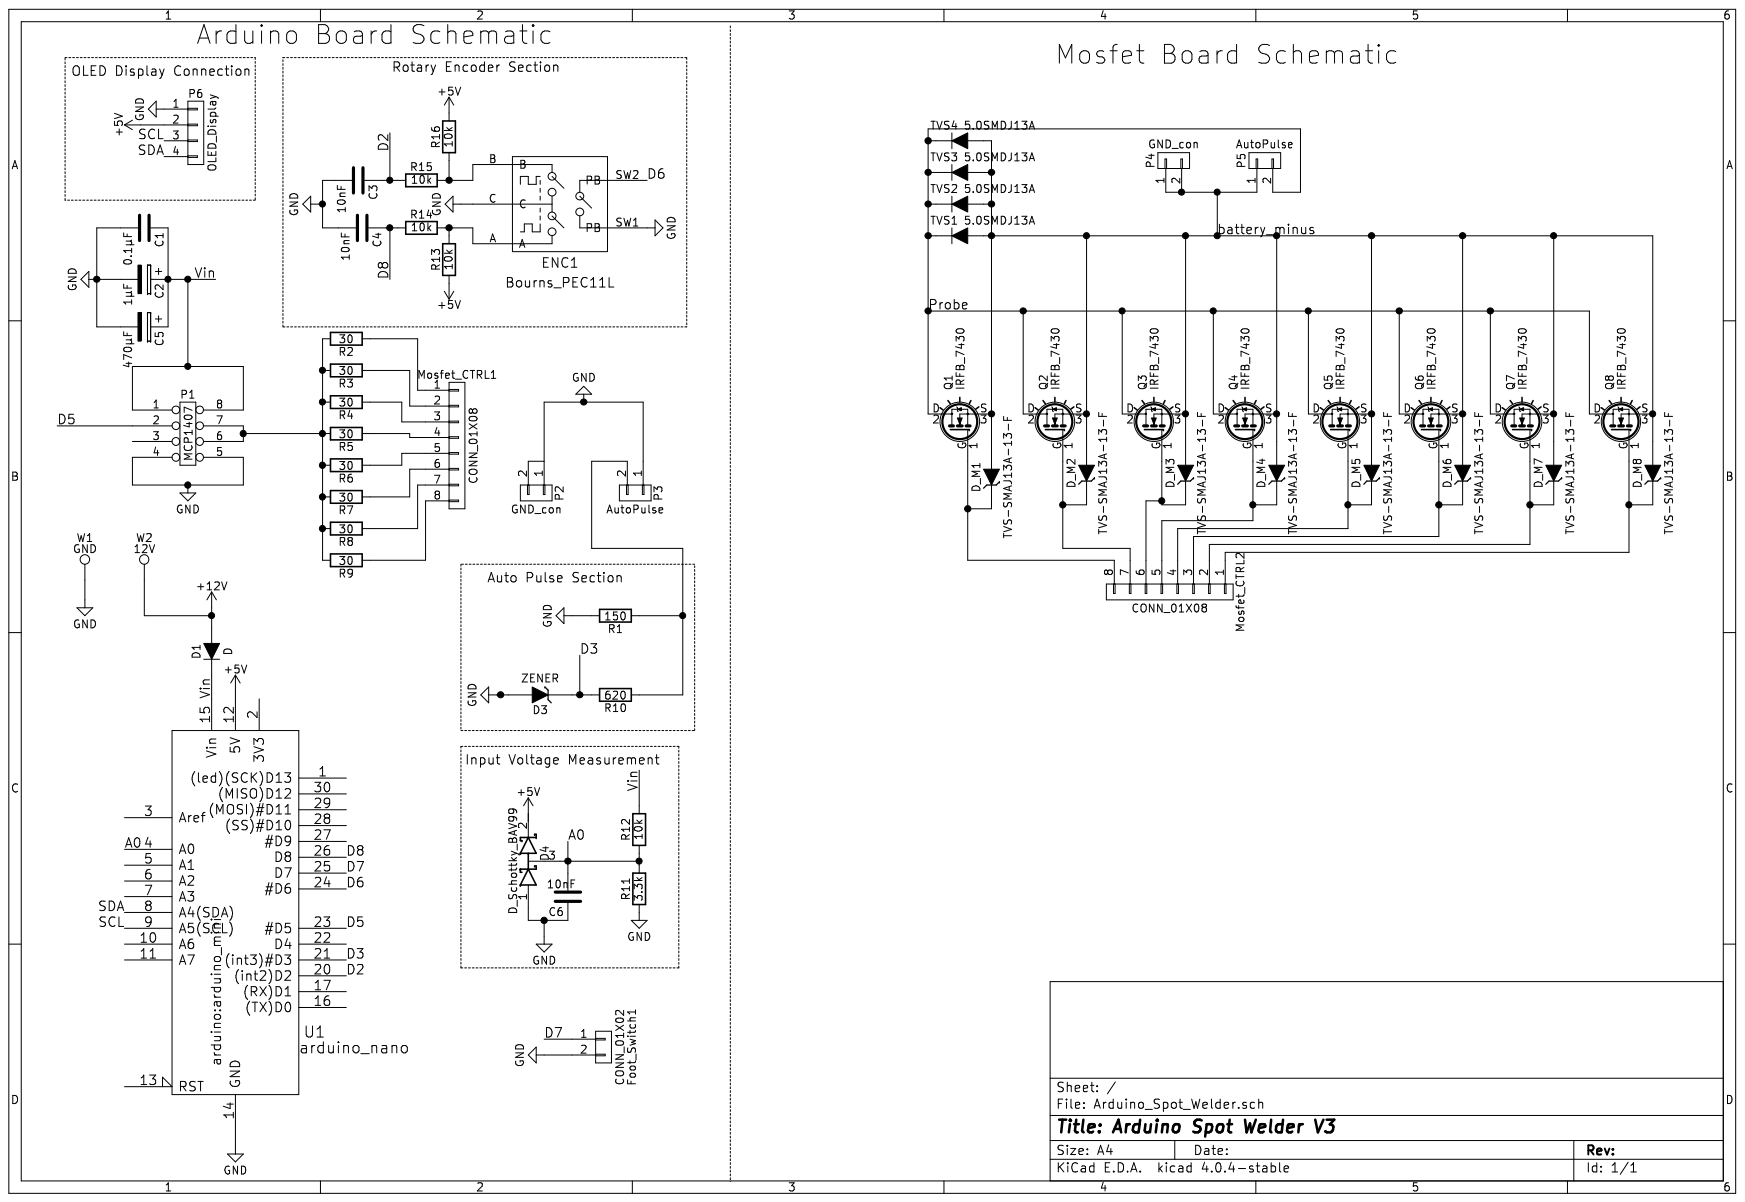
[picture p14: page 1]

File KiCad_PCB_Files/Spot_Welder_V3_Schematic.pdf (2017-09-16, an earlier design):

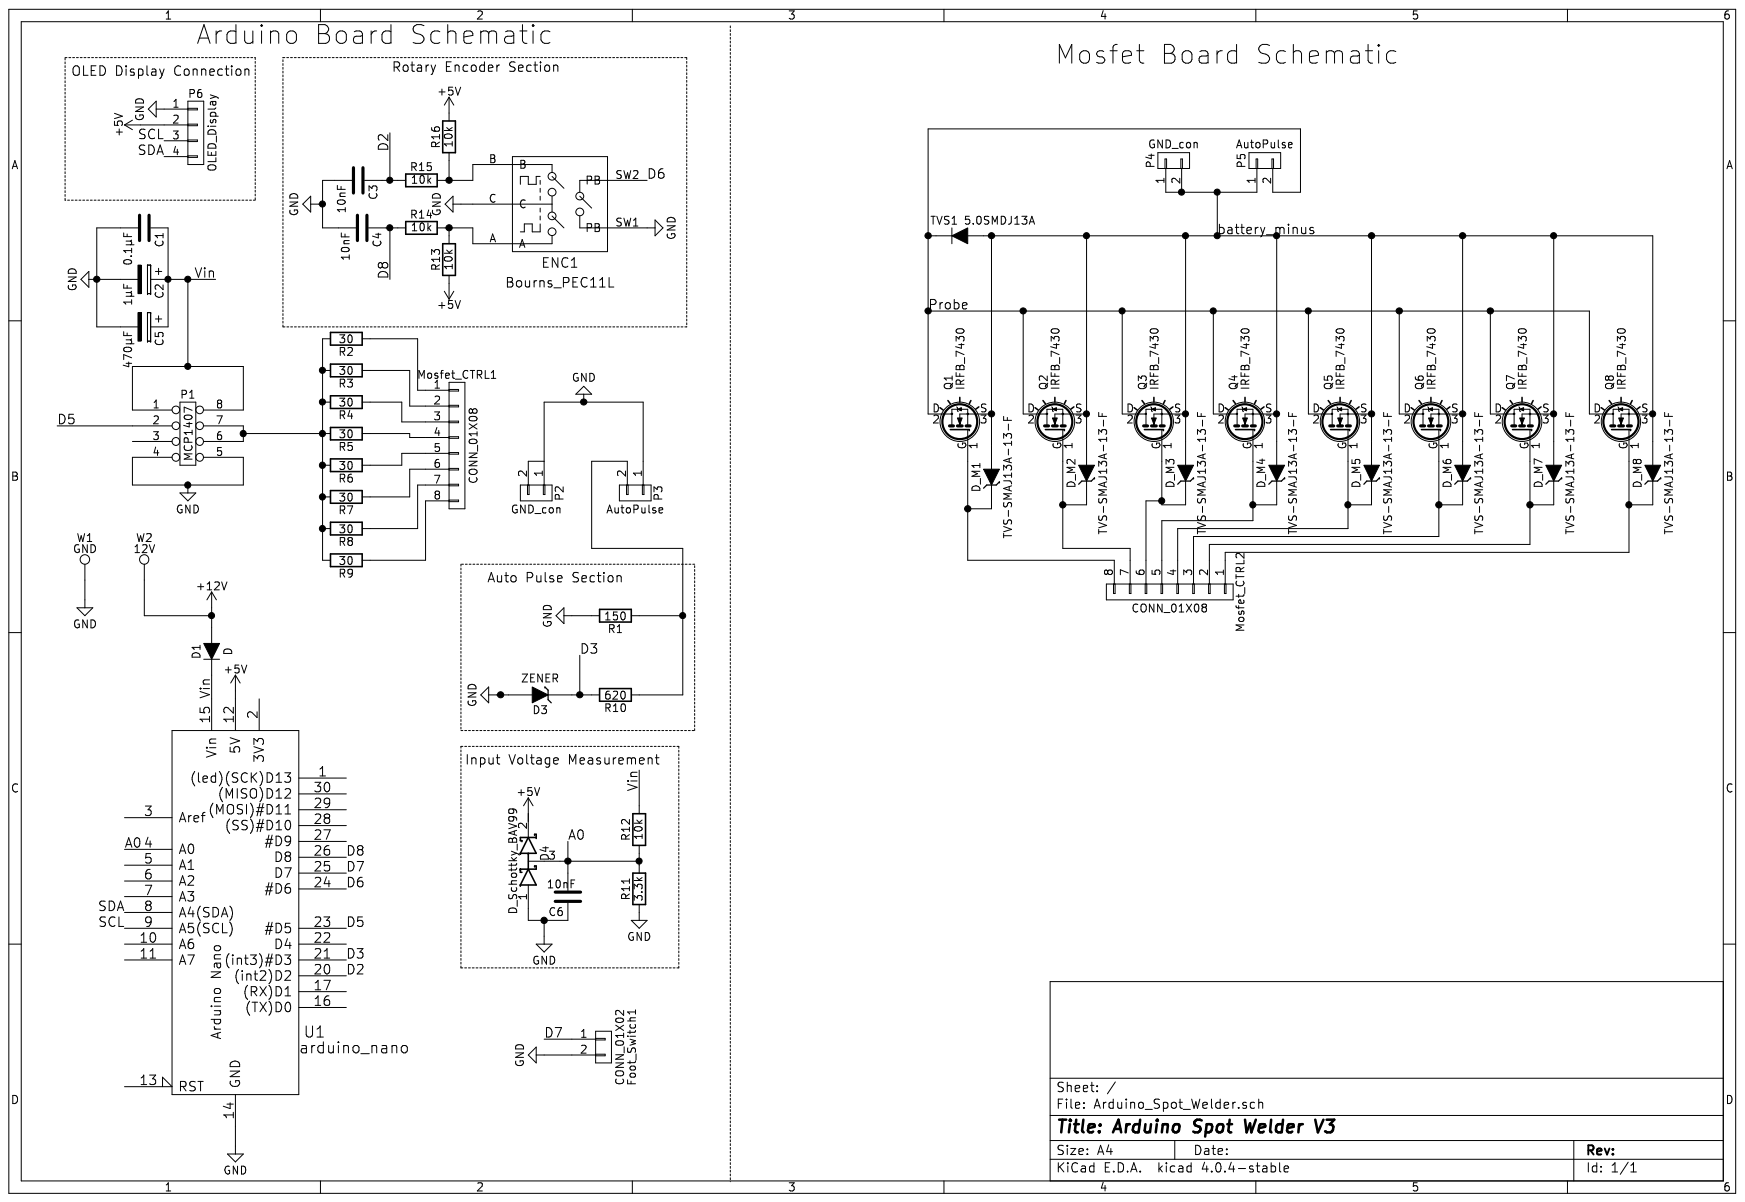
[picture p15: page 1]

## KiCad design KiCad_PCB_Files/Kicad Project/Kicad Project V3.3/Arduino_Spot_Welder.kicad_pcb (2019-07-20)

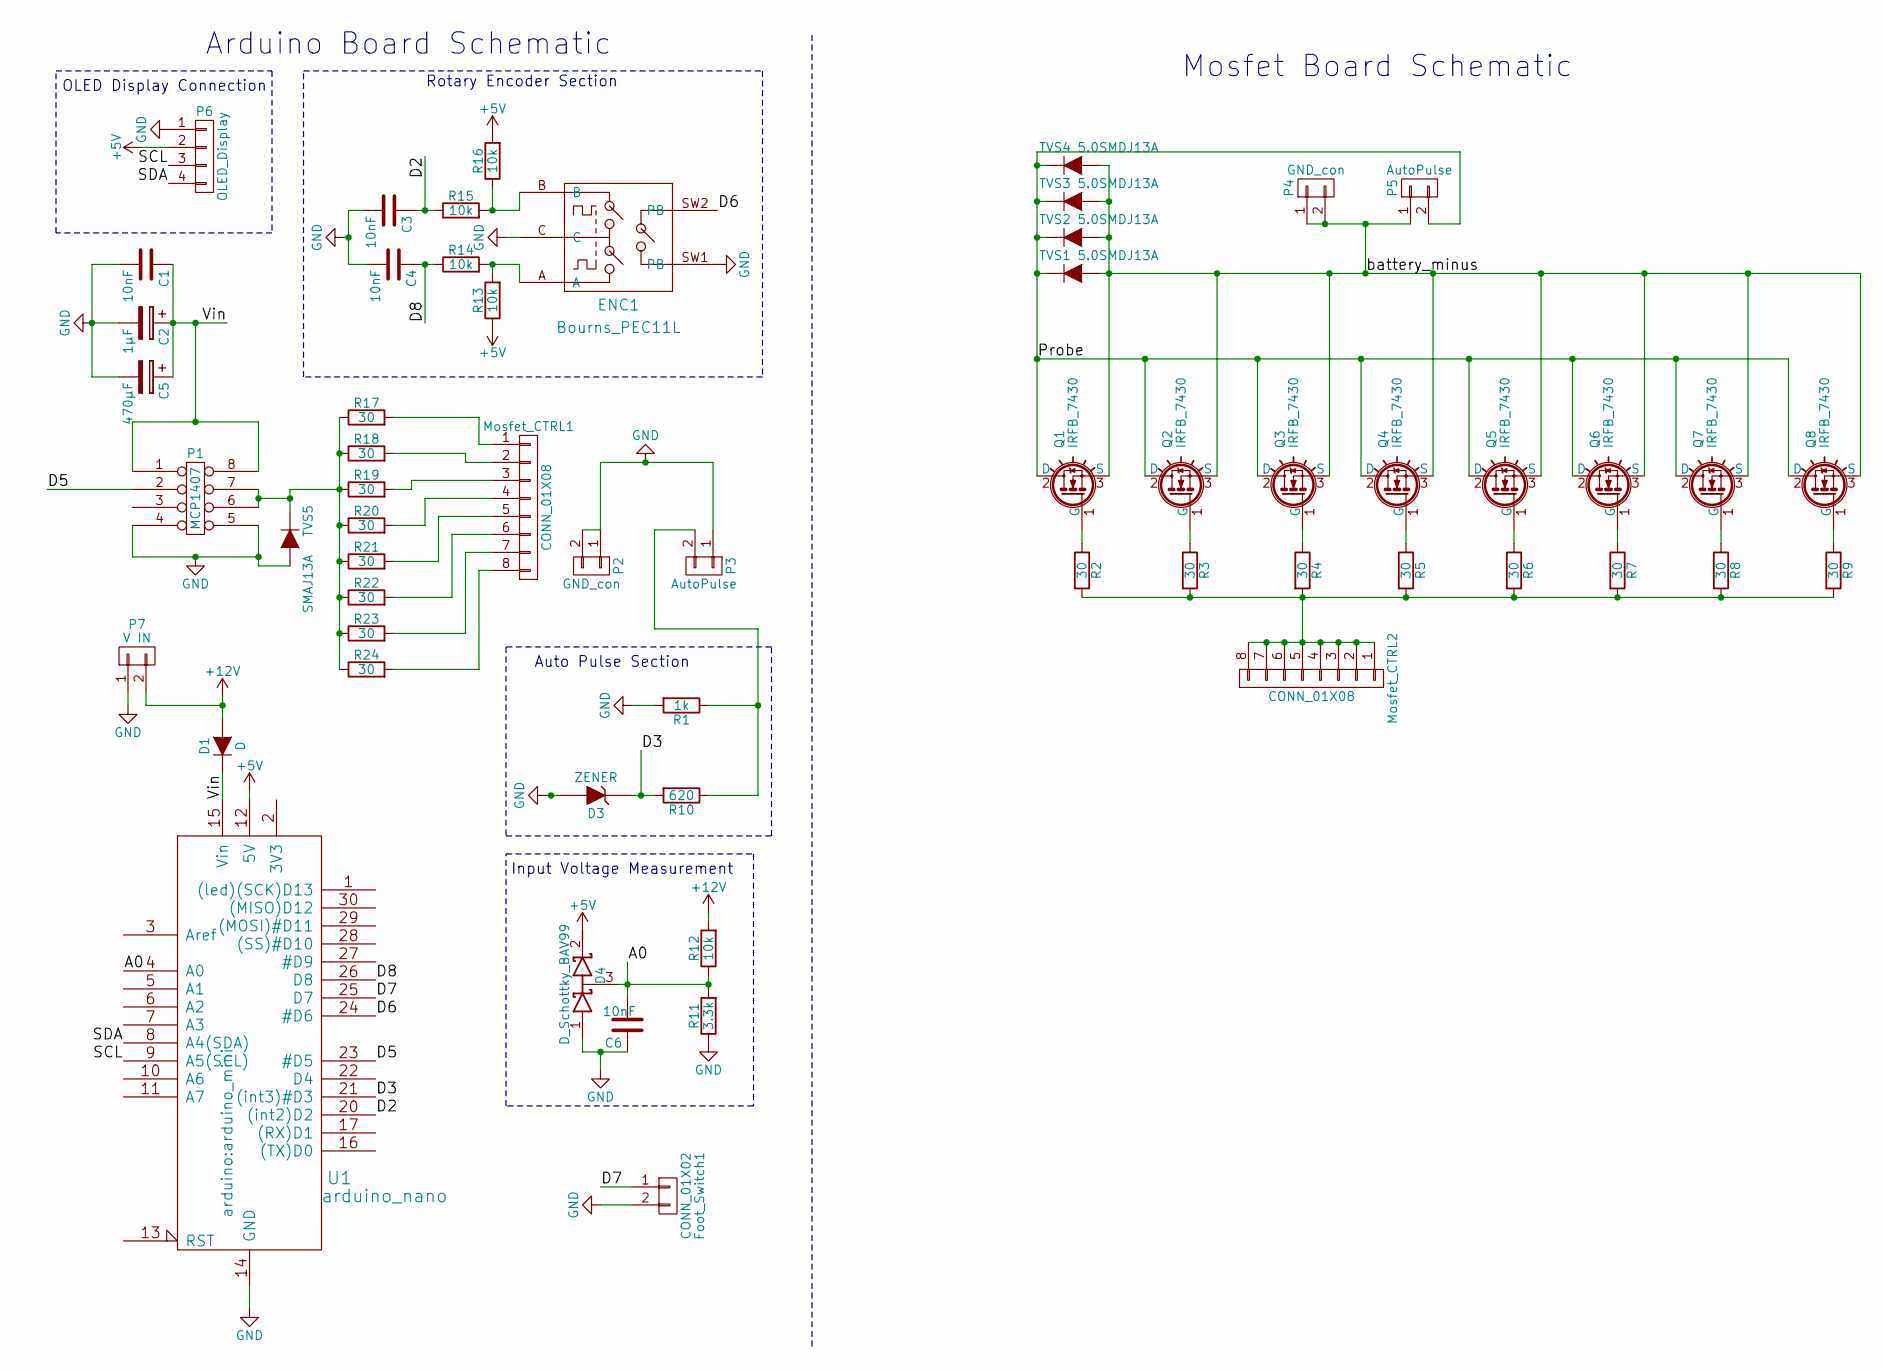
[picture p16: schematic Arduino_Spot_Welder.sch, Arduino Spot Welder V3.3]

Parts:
C1, C3, C4, C6: 10nF; C_1210_HandSoldering
C2: 1µF; C_Disc_D7.5mm_W5.0mm_P5.00mm
C5: 470µF; CP_Elec_10x10
D1: D; D_SMA_Handsoldering
D3: ZENER; D_SOD-123
D4: D_Schottky_BAV99; SOT-23
ENC1: Bourns_PEC11L; ALPS_STEC12E08
Foot_Switch1: CONN_01X02; Molex_KK-6410-02_02x2.54mm_Straight
Mosfet_CTRL1, Mosfet_CTRL2: CONN_01X08; Pin_Header_Straight_1x08_Pitch2.54mm_Large_Pads
P1: MCP1407; DIP-8_W7.62mm_Socket_LongPads
P2, P4: GND_con; Pin_Header_Straight_1x02_Pitch2.54mm
P3, P5: AutoPulse; Pin_Header_Straight_1x02_Pitch2.54mm
P6: OLED_Display; OLED_SSD1306_128x64
P7: V IN; Terminal_Block_2P_3.5mm; MFG Part Number Value
Q1, Q2, Q3, Q4, Q5, Q6, Q7, Q8: IRFB_7430; TO-220__long_Neutral123_Horizontal_LargePads
R1: 1k; R_1206_HandSoldering; MFG Part Number Value
R2, R3, R4, R5, R6, R7, R8, R9, R17, R18, R19, R20, R21, R22, R23, R24: 30; R_1206_HandSoldering
R10: 620; R_1206_HandSoldering
R11: 3.3k; R_1206_HandSoldering
R12, R13, R14, R15, R16: 10k; R_1206_HandSoldering
TVS1, TVS2, TVS3, TVS4: 5.0SMDJ13A; D_SMC_Handsoldering
TVS5: SMAJ13A; D_SMA; MFG Part Number SMAJ13A-13-F
U1: arduino_nano; arduino_mini

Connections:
+5V: D4.2 (K), P6.2, R13.1, R16.2, U1.12 (5V)
+12V: D1.2 (A), P7.2, R12.2
/A0: C6.2, D4.3 (common), R11.2, R12.1, U1.4 (A0)
/D2: C3.1, R15.1, U1.20 ((int2)D2)
/D3: D3.1 (K), R10.2, U1.21 ((int3)#D3)
/D5: P1.2, U1.23 (#D5)
/D6: ENC1.SW2 (PB), U1.24 (#D6)
/D7: Foot_Switch1.1, U1.25 (D7)
/D8: C4.1, R14.1, U1.26 (D8)
/Probe: P5.2, Q1.2 (D), Q2.2 (D), Q3.2 (D), Q4.2 (D), Q5.2 (D), Q6.2 (D), Q7.2 (D), Q8.2 (D), TVS1.1 (K), TVS2.1 (K), TVS3.1 (K), TVS4.1 (K)
/SCL: P6.3, U1.9 (A5(SCL))
/SDA: P6.4, U1.8 (A4(SDA))
/Vin: C1.1, C2.1, C5.1, D1.1 (K), P1.1, P1.8, U1.15 (Vin)
/battery_minus: P4.1, P4.2, P5.1, Q1.3 (S), Q2.3 (S), Q3.3 (S), Q4.3 (S), Q5.3 (S), Q6.3 (S), Q7.3 (S), Q8.3 (S), TVS1.2 (A), TVS2.2 (A), TVS3.2 (A), TVS4.2 (A)
GND: C1.2, C2.2, C3.2, C4.2, C5.2, C6.1, D3.2 (A), D4.1 (A), ENC1.C, ENC1.SW1 (PB), Foot_Switch1.2, P1.4, P1.5, P2.1, P2.2, P3.1, P6.1, P7.1, R1.2, R11.1, TVS5.2 (A), U1.14 (GND), U1.19 (GND)
unnamed: ENC1.A, R13.2, R14.2
unnamed: ENC1.B, R15.2, R16.1
unnamed: Mosfet_CTRL1.1, R17.2
unnamed: Mosfet_CTRL1.2, R18.2
unnamed: Mosfet_CTRL1.3, R19.2
unnamed: Mosfet_CTRL1.4, R20.2
unnamed: Mosfet_CTRL1.5, R21.2
unnamed: Mosfet_CTRL1.6, R22.2
unnamed: Mosfet_CTRL1.7, R23.2
unnamed: Mosfet_CTRL1.8, R24.2
unnamed: Mosfet_CTRL2.1, Mosfet_CTRL2.2, Mosfet_CTRL2.3, Mosfet_CTRL2.4, Mosfet_CTRL2.5, Mosfet_CTRL2.6, Mosfet_CTRL2.7, Mosfet_CTRL2.8, R2.2, R3.2, R4.2, R5.2, R6.2, R7.2, R8.2, R9.2
unnamed: P1.6, P1.7, R17.1, R18.1, R19.1, R20.1, R21.1, R22.1, R23.1, R24.1, TVS5.1 (K)
unnamed: P3.2, R1.1, R10.1
unnamed: Q1.1 (G), R2.1
unnamed: Q2.1 (G), R3.1
unnamed: Q3.1 (G), R4.1
unnamed: Q4.1 (G), R5.1
unnamed: Q5.1 (G), R6.1
unnamed: Q6.1 (G), R7.1
unnamed: Q7.1 (G), R8.1
unnamed: Q8.1 (G), R9.1

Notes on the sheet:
Arduino Board Schematic
Mosfet Board Schematic
Auto Pulse Section
OLED Display Connection
Rotary Encoder Section
Input Voltage Measurement

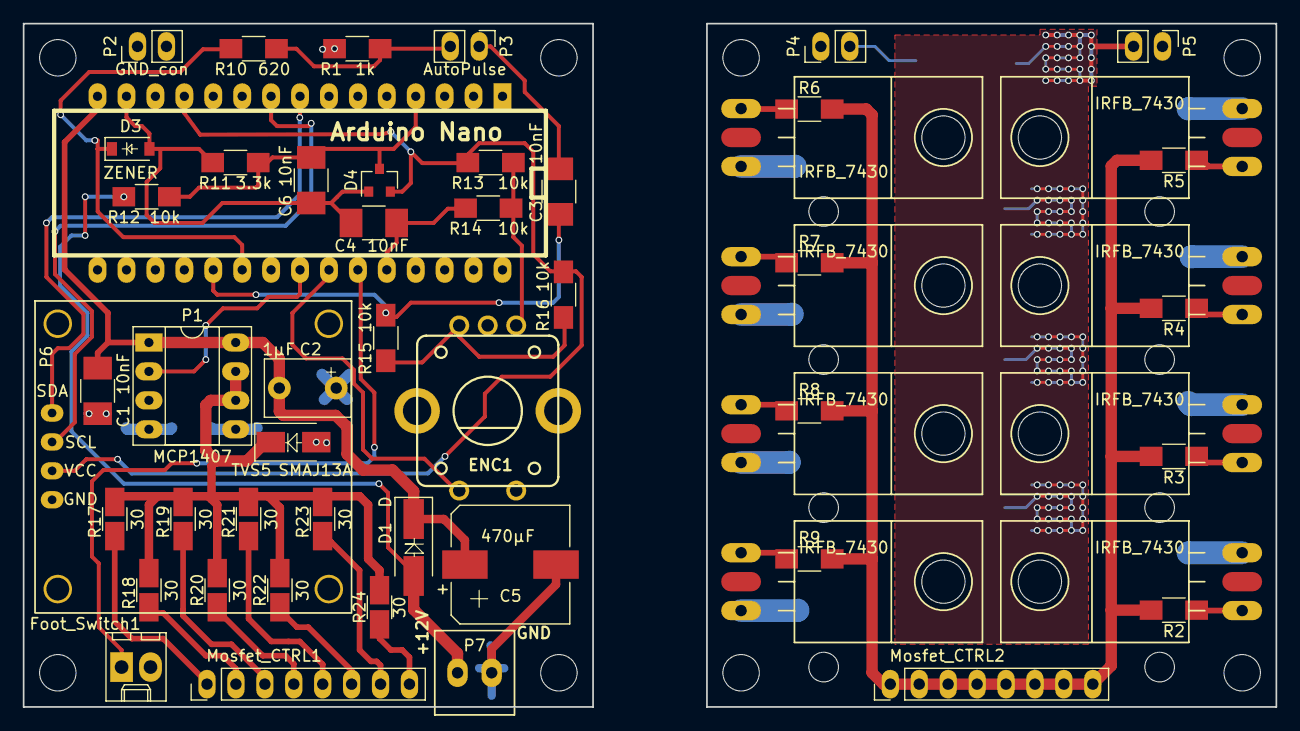
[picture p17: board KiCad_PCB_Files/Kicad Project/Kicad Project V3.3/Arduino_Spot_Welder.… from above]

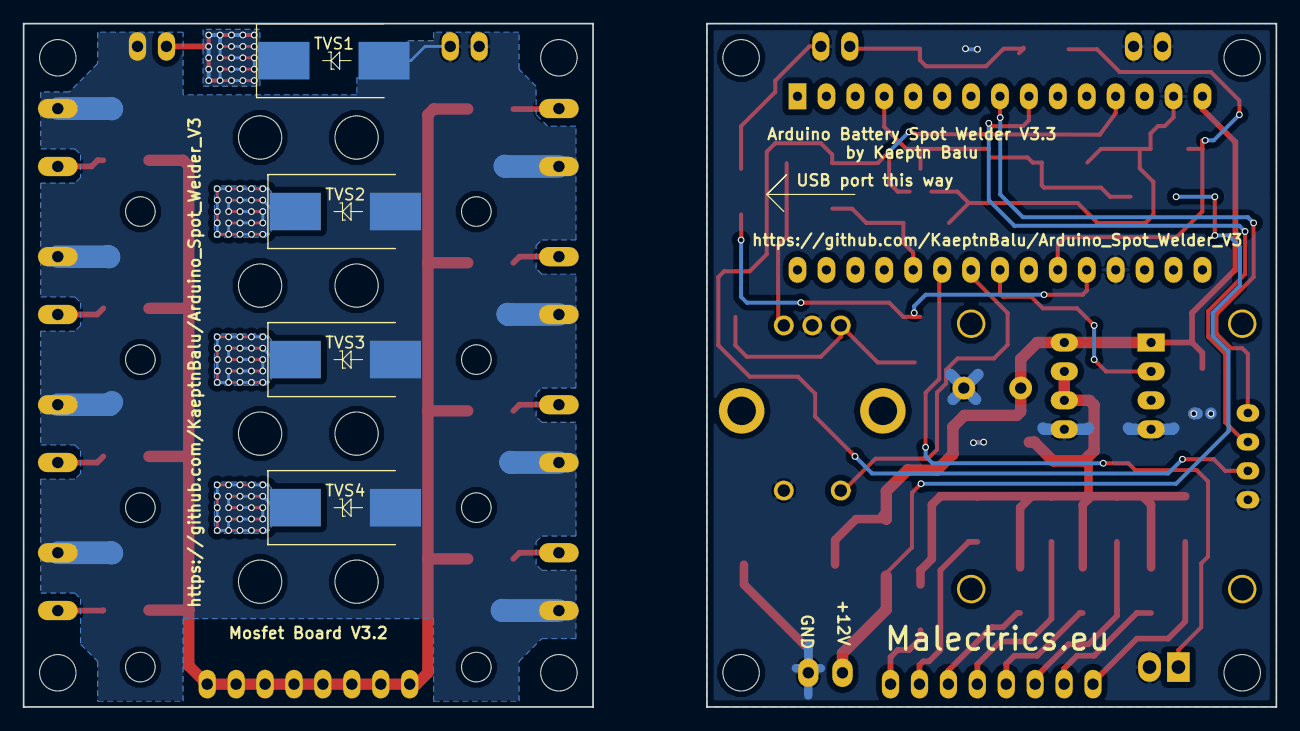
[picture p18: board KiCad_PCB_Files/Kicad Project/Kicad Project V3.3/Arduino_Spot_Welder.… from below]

Board: 2 copper layers, 110.0 x 60.0 mm, 58 parts (4 on the bottom side), 36 nets.

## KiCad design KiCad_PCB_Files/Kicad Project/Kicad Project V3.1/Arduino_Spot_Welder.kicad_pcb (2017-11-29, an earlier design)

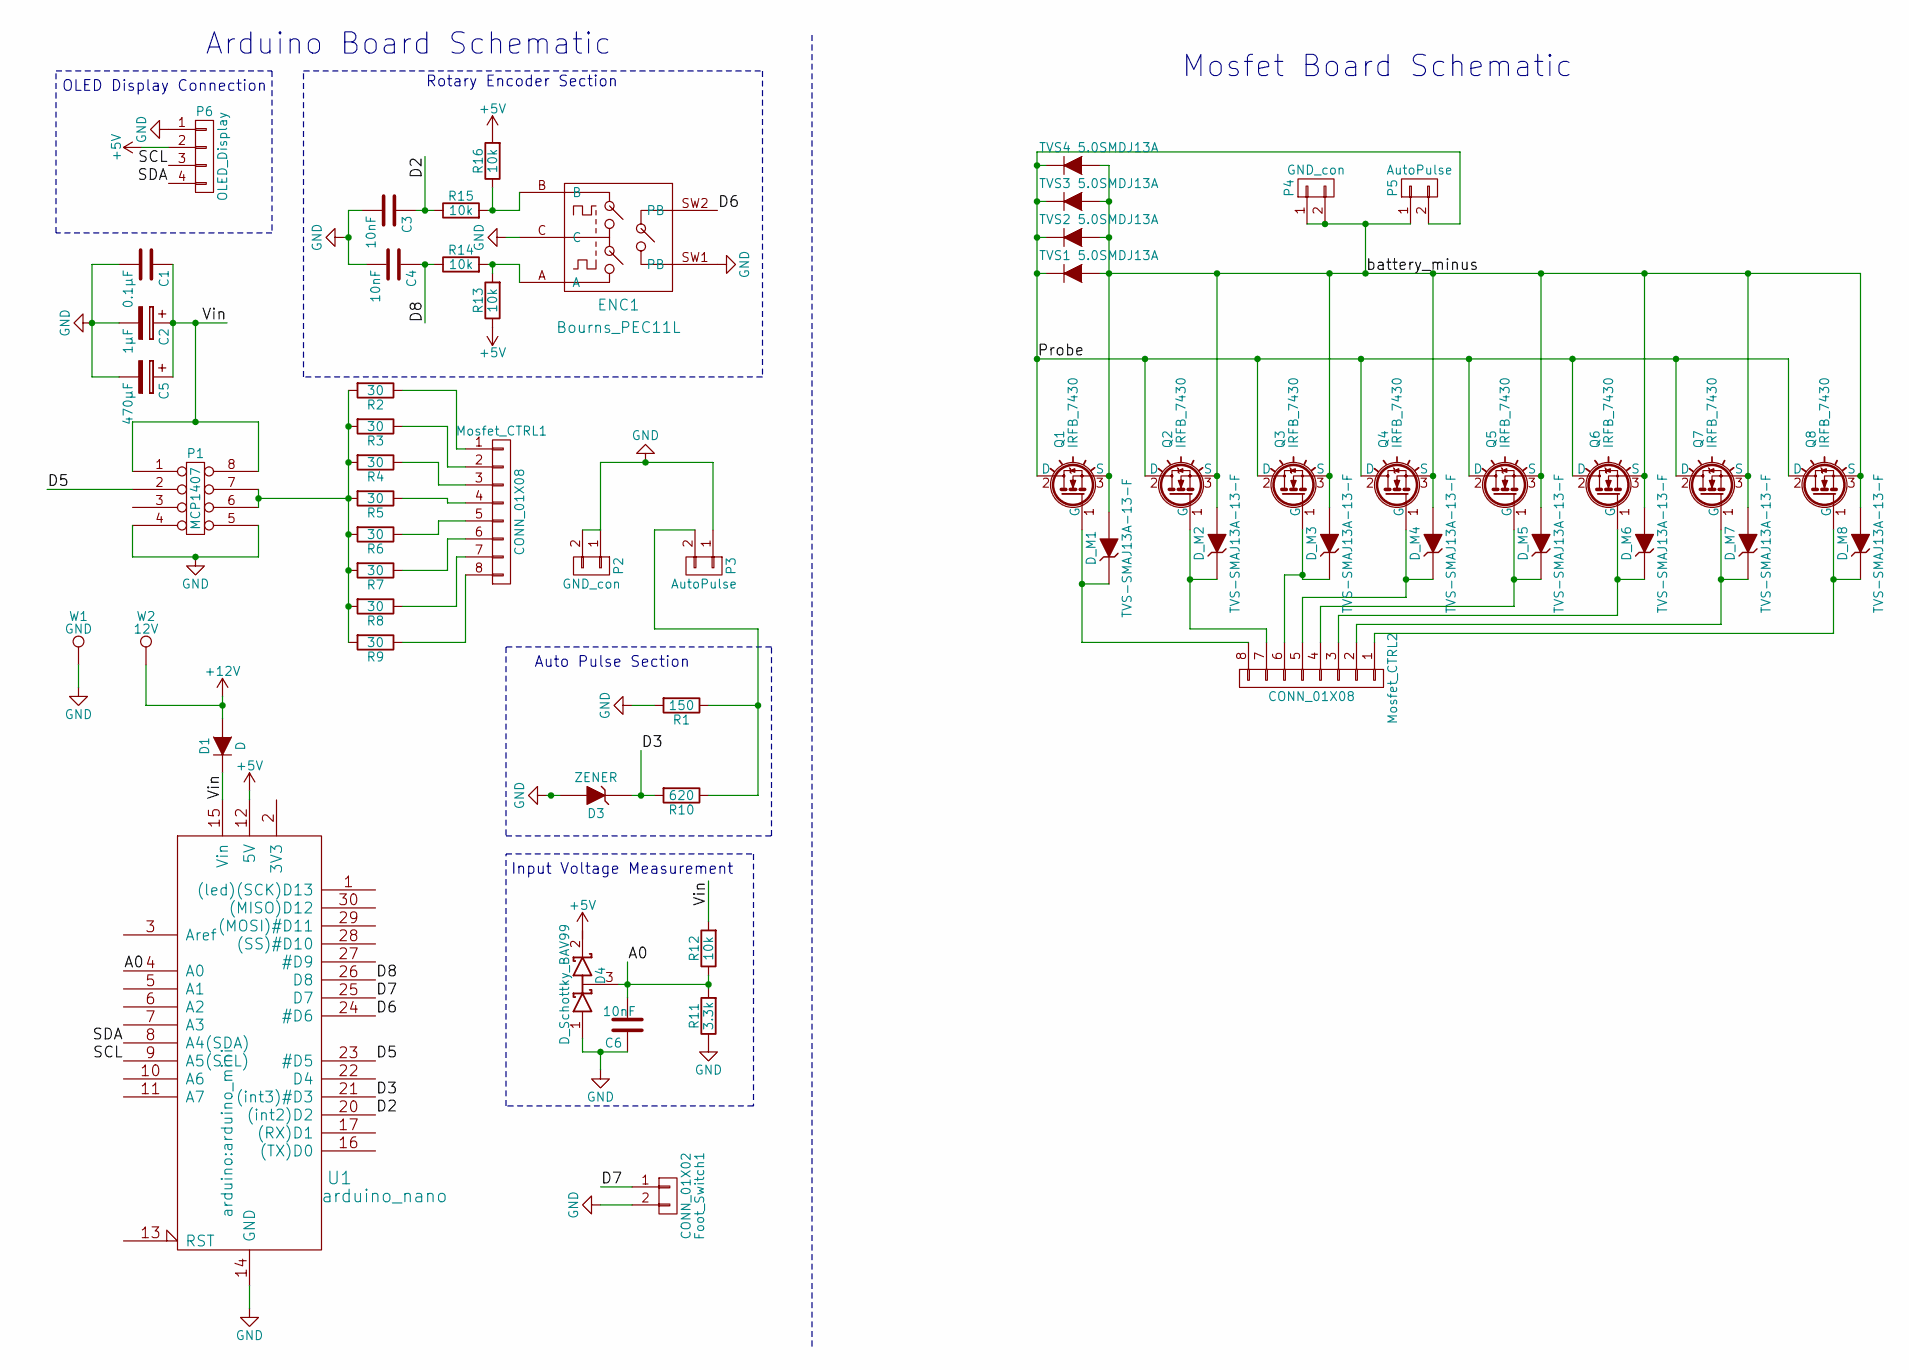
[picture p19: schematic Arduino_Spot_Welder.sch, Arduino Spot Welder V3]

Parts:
C1: 0.1µF; C_1210_HandSoldering
C2: 1µF; C_Disc_D7.5mm_W5.0mm_P5.00mm
C3, C4, C6: 10nF; C_1210_HandSoldering
C5: 470µF; CP_Elec_10x10
D1: D; D_SMA_Handsoldering
D3: ZENER; D_MiniMELF_Handsoldering
D4: D_Schottky_BAV99; SOT-23
D_M1, D_M2, D_M3, D_M4, D_M5, D_M6, D_M7, D_M8: TVS-SMAJ13A-13-F; D_SMA
ENC1: Bourns_PEC11L; ALPS_STEC12E08
Foot_Switch1: CONN_01X02; Molex_KK-6410-02_02x2.54mm_Straight
Mosfet_CTRL1, Mosfet_CTRL2: CONN_01X08; Pin_Header_Straight_1x08_Pitch2.54mm_Large_Pads
P1: MCP1407; DIP-8_W7.62mm_Socket_LongPads
P2, P4: GND_con; Pin_Header_Straight_1x02_Pitch2.54mm
P3, P5: AutoPulse; Pin_Header_Straight_1x02_Pitch2.54mm
P6: OLED_Display; OLED_SSD1306_128x64
Q1, Q2, Q3, Q4, Q5, Q6, Q7, Q8: IRFB_7430; TO-220__long_Neutral123_Horizontal_LargePads
R1: 150; R_2512_HandSoldering
R2, R3, R4, R5, R6, R7, R8, R9: 30; R_1206_HandSoldering
R10: 620; R_1206_HandSoldering
R11: 3.3k; R_1206_HandSoldering
R12, R13, R14, R15, R16: 10k; R_1206_HandSoldering
TVS1, TVS2, TVS3, TVS4: 5.0SMDJ13A; D_SMC_Handsoldering
U1: arduino_nano; arduino_mini
W1: GND; SolderWirePad_single_1mmDrill
W2: 12V; SolderWirePad_single_1mmDrill

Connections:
+5V: D4.2 (K), P6.2, R13.1, R16.2, U1.12 (5V)
+12V: D1.2 (A), W2.1
/A0: C6.2, D4.3 (common), R11.2, R12.1, U1.4 (A0)
/D2: C3.1, R15.1, U1.20 ((int2)D2)
/D3: D3.1 (K), R10.2, U1.21 ((int3)#D3)
/D5: P1.2, U1.23 (#D5)
/D6: ENC1.SW2 (PB), U1.24 (#D6)
/D7: Foot_Switch1.1, U1.25 (D7)
/D8: C4.1, R14.1, U1.26 (D8)
/Probe: P5.2, Q1.2 (D), Q2.2 (D), Q3.2 (D), Q4.2 (D), Q5.2 (D), Q6.2 (D), Q7.2 (D), Q8.2 (D), TVS1.1 (K), TVS2.1 (K), TVS3.1 (K), TVS4.1 (K)
/SCL: P6.3, U1.9 (A5(SCL))
/SDA: P6.4, U1.8 (A4(SDA))
/Vin: C1.1, C2.1, C5.1, D1.1 (K), P1.1, P1.8, R12.2, U1.15 (Vin)
/battery_minus: D_M1.2 (A), D_M2.2 (A), D_M3.2 (A), D_M4.2 (A), D_M5.2 (A), D_M6.2 (A), D_M7.2 (A), D_M8.2 (A), P4.1, P4.2, P5.1, Q1.3 (S), Q2.3 (S), Q3.3 (S), Q4.3 (S), Q5.3 (S), Q6.3 (S), Q7.3 (S), Q8.3 (S), TVS1.2 (A), TVS2.2 (A), TVS3.2 (A), TVS4.2 (A)
GND: C1.2, C2.2, C3.2, C4.2, C5.2, C6.1, D3.2 (A), D4.1 (A), ENC1.C, ENC1.SW1 (PB), Foot_Switch1.2, P1.4, P1.5, P2.1, P2.2, P3.1, P6.1, R1.2, R11.1, U1.14 (GND), U1.19 (GND), W1.1
unnamed: D_M1.1 (K), Mosfet_CTRL2.8, Q1.1 (G)
unnamed: D_M2.1 (K), Mosfet_CTRL2.7, Q2.1 (G)
unnamed: D_M3.1 (K), Mosfet_CTRL2.6, Q3.1 (G)
unnamed: D_M4.1 (K), Mosfet_CTRL2.5, Q4.1 (G)
unnamed: D_M5.1 (K), Mosfet_CTRL2.4, Q5.1 (G)
unnamed: D_M6.1 (K), Mosfet_CTRL2.3, Q6.1 (G)
unnamed: D_M7.1 (K), Mosfet_CTRL2.2, Q7.1 (G)
unnamed: D_M8.1 (K), Mosfet_CTRL2.1, Q8.1 (G)
unnamed: ENC1.A, R13.2, R14.2
unnamed: ENC1.B, R15.2, R16.1
unnamed: Mosfet_CTRL1.1, R2.1
unnamed: Mosfet_CTRL1.2, R3.1
unnamed: Mosfet_CTRL1.3, R4.1
unnamed: Mosfet_CTRL1.4, R5.1
unnamed: Mosfet_CTRL1.5, R6.1
unnamed: Mosfet_CTRL1.6, R7.1
unnamed: Mosfet_CTRL1.7, R8.1
unnamed: Mosfet_CTRL1.8, R9.1
unnamed: P1.6, P1.7, R2.2, R3.2, R4.2, R5.2, R6.2, R7.2, R8.2, R9.2
unnamed: P3.2, R1.1, R10.1

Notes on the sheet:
Arduino Board Schematic
Mosfet Board Schematic
Auto Pulse Section
OLED Display Connection
Rotary Encoder Section
Input Voltage Measurement

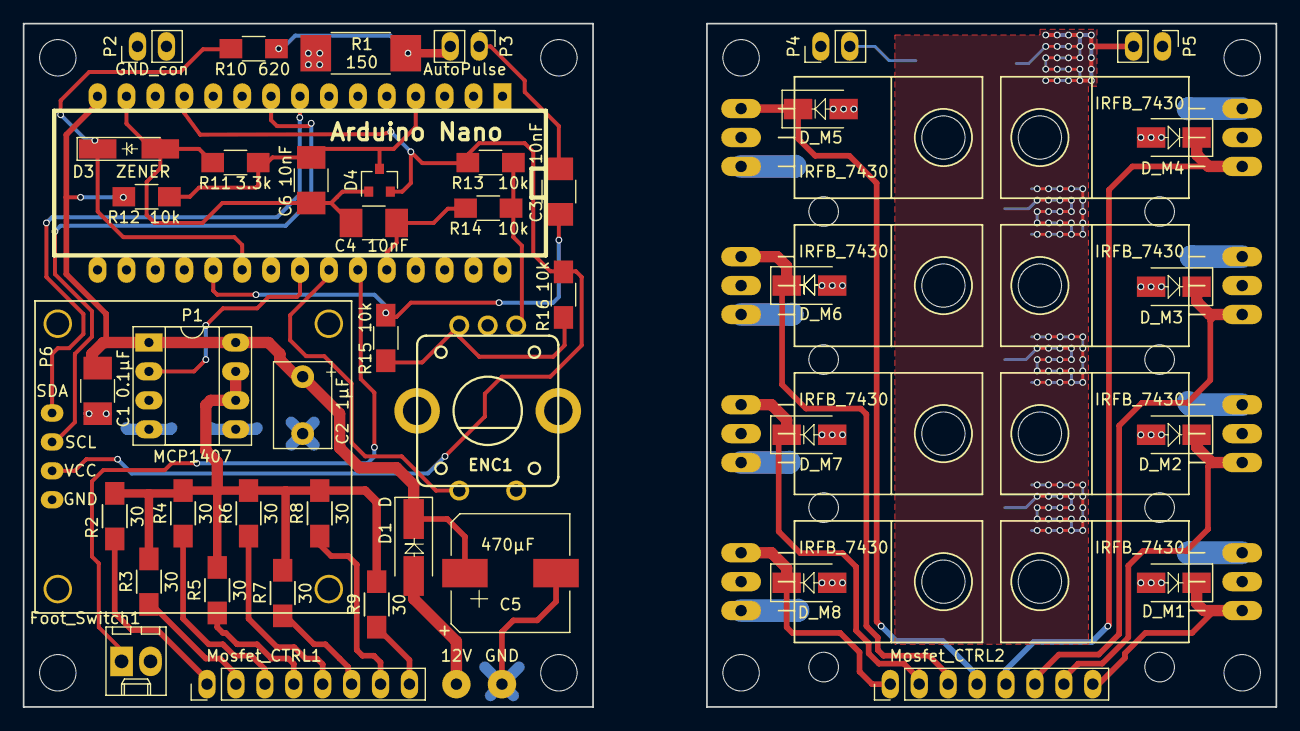
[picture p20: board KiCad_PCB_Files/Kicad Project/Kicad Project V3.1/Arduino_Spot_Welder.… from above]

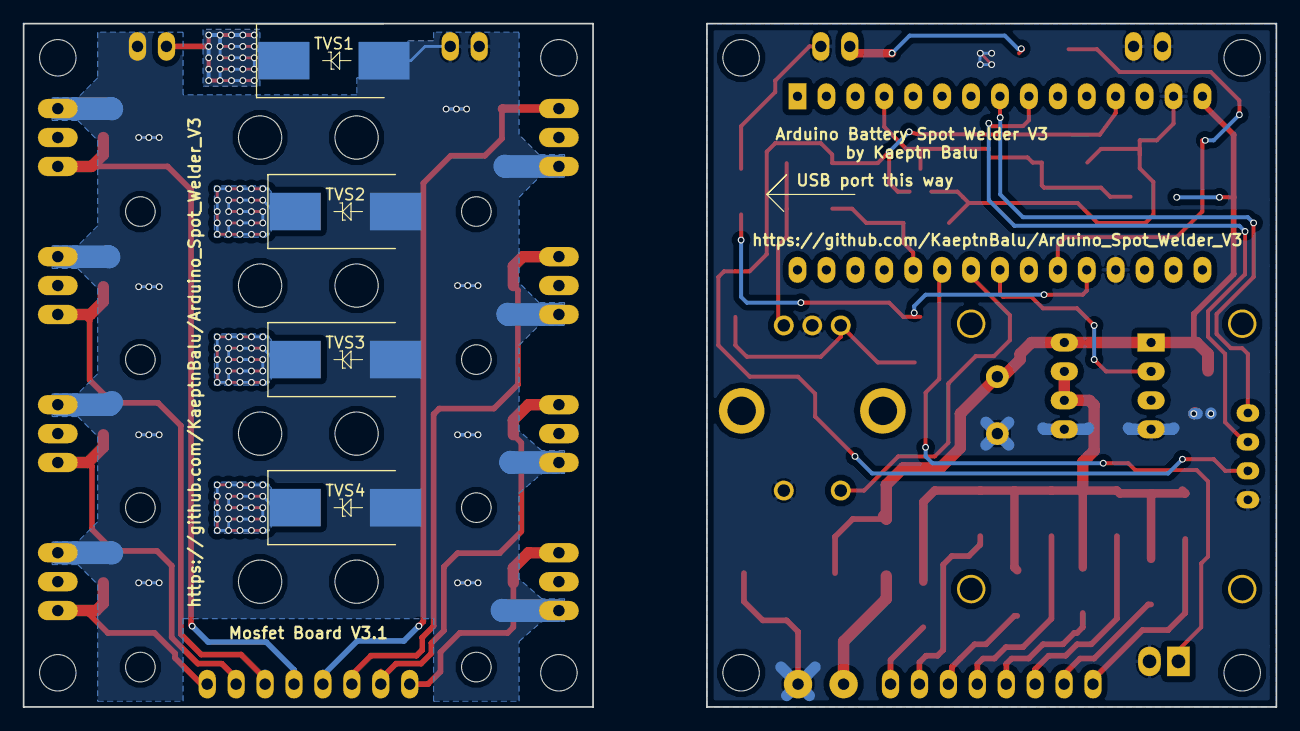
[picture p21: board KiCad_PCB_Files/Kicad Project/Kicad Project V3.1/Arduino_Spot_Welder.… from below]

Board: 2 copper layers, 110.0 x 60.0 mm, 58 parts (4 on the bottom side), 35 nets.

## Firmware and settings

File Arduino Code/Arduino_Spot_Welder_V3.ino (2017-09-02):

/*=======================================================================================
                                    Includes
========================================================================================*/

#include <Wire.h>
#include <Adafruit_GFX.h>
#include <Adafruit_SSD1306.h>
#include <EEPROM.h>

/*=======================================================================================
                                User Configurarations
========================================================================================*/
#define	_STANDBY_TIME_OUT	(300000)	//in mSeconds

const int EEPROM_MIN_ADDR = 0;
const int EEPROM_MAX_ADDR = 511;

/*=======================================================================================
                                    Definitions
========================================================================================*/
#define _ENCODER_EN

#define STANDBY 				0
#define MAIN_SCREEN 		1
#define MAIN_SCREEN_CNT 2
#define MENU_SCREEN 		3
#define SUB_MENU_1 			4
#define SUB_MENU_2 			5
#define BATTERY_LOW			6

/*=======================================================================================
                          Pin definitions and variables
========================================================================================*/
const int PinCLK	= 2; 	// Used for generating interrupts using CLK signal
const int PinDT		= 8;  // Used for reading DT signal
const int PinSW		= 6;  // Used for the push button switch

const int PinFootSwitch		= 7;
const int PinAutoPulse		= 3;

const int PinPulse				= 5;
const int PinLED					= 4;

const int PinBatVol				= A0;

/*=======================================================================================
                       OLED Display Configurarions and variables
========================================================================================*/
#define OLED_RESET 4
Adafruit_SSD1306 display(OLED_RESET);

#define NUMFLAKES 10
#define XPOS 			0
#define YPOS 			1
#define DELTAY 		2

#define LOGO16_GLCD_HEIGHT 64
#define LOGO16_GLCD_WIDTH  128 
static const unsigned char PROGMEM logo16_glcd_bmp[] =
{ B00000000, B11000000,
  B00000001, B11000000,
  B00000001, B11000000,
  B00000011, B11100000,
  B11110011, B11100000,
  B11111110, B11111000,
  B01111110, B11111111,
  B00110011, B10011111,
  B00011111, B11111100,
  B00001101, B01110000,
  B00011011, B10100000,
  B00111111, B11100000,
  B00111111, B11110000,
  B01111100, B11110000,
  B01110000, B01110000,
  B00000000, B00110000 };

#if (SSD1306_LCDHEIGHT != 64)
#error("Height incorrect, please fix Adafruit_SSD1306.h!");
#endif


/*=======================================================================================
                                  Globle Variables
========================================================================================*/
long lastVirtualPosition = 0;
uint8_t selectedMenu = 0;
uint8_t State = MAIN_SCREEN;
uint8_t lastBatterVoltage = 0;
uint16_t lastWeldCount = 0, lastPulseDelay = 0;

uint8_t BatteryVoltage = 124;

typedef struct AllData{
	uint8_t delay;
	uint8_t batteryAlarm;
	uint16_t weldCount;
	uint16_t pulseDelay;
	uint8_t shortPulse;
	uint8_t autoPulse;

}allData;

allData gAllData;

uint8_t Delay 				= 20;
uint8_t BatteryAlarm 	= 110;
uint16_t WeldCount 		= 0;
uint16_t PulseDelay 	= 5;
uint8_t ShortPulse 		= 12;
uint8_t AutoPulse 		= 1;

long VirtualPosition = 0;
static unsigned long lastInterruptTime = 0;

unsigned long lastActiveTime;
unsigned long previousMillis = 0; 
unsigned long interval = 1000;    


/*=======================================================================================
                                   Setup function
========================================================================================*/
void setup()   {                
  Serial.begin(9600);

  pinMode(PinCLK,INPUT);
  pinMode(PinDT,INPUT);  
  
  pinMode(PinSW,INPUT_PULLUP);
  digitalWrite(PinSW,HIGH);
  
  attachInterrupt (0,isr,FALLING);   // interrupt 0 is always connected to pin 2 on Arduino UNO
	
	pinMode(PinLED,OUTPUT);
	pinMode(PinPulse,OUTPUT);
	
	pinMode(PinFootSwitch,INPUT_PULLUP);
	digitalWrite(PinFootSwitch,HIGH);
	
	pinMode(PinAutoPulse,INPUT);
	//digitalWrite(PinAutoPulse,LOW);

  // by default, we'll generate the high voltage from the 3.3v line internally! (neat!)
  display.begin(SSD1306_SWITCHCAPVCC, 0x3C);  
  
  display.clearDisplay();
  display.display();	
	lastActiveTime = millis();
	lastVirtualPosition = VirtualPosition;
	
	
	
	gAllData.delay 				= 20;
	gAllData.batteryAlarm = 110;
	gAllData.weldCount 		= 0;
	gAllData.pulseDelay 	= 5;
	gAllData.shortPulse		= 12;
	gAllData.autoPulse		= 1;
	
	byte tmpArraEe[10],tmp2ArrEe[10];
	eeprom_read_bytes(0,tmpArraEe,8);
	
	if( memcmp(tmpArraEe,&gAllData,8) != 0){
		if( tmpArraEe[6] == 0xFF ){
			memcpy(tmp2ArrEe, &gAllData,8);
			eeprom_write_bytes(0,tmp2ArrEe,8);
		}
		else{	
			memcpy(&gAllData,tmpArraEe,8);
		}
	}
	eepromReset();
	
	//Serial.println(gAllData.delay);
	//Serial.println(gAllData.batteryAlarm);
	//Serial.println(gAllData.weldCount);
	//Serial.println(gAllData.pulseDelay);
	//Serial.println(gAllData.shortPulse);
	//Serial.println(gAllData.autoPulse);
	
	Delay					=		gAllData.delay 				;
	BatteryAlarm	=		gAllData.batteryAlarm ;
	WeldCount			=		gAllData.weldCount 		;
	PulseDelay		=		gAllData.pulseDelay 	;
	ShortPulse		=		gAllData.shortPulse		;
	AutoPulse			=		gAllData.autoPulse		;
	
}

/*=======================================================================================
                                            Loop
========================================================================================*/
void loop(){	
	StateMachine();
	CheckForSleep();
	CheckBatteryVoltage();
	updateEeprom();
	
	if(State==MAIN_SCREEN_CNT){

//------------------------Pulse activated with AutoPulse feature-------------------------
		if(digitalRead(PinAutoPulse) && (AutoPulse == 0)){
			//auto pulse activate			
      delay(Delay*100);
			sendPulse();
			  // Wait until switch has been released
        do {
        digitalWrite(PinPulse, LOW);
        } while (digitalRead(PinAutoPulse));
      // Delay before impulse can be triggered again
      delay(500);			
		}

//------------------------Pulse activated with Foot switch-------------------------------
		if(!digitalRead(PinFootSwitch)){
			//pulse activated;
     delay(200);
		 sendPulse();
        do {
        digitalWrite(PinPulse, LOW);
        }
			  while(!digitalRead(PinFootSwitch));
     // Delay before impulse can be triggered again
     delay(500);
		}
	}
}

/*=======================================================================================
                                         Functions
========================================================================================*/

void eepromReset(){
	if( encBtnState()==LOW ){
		byte tmpArraEe[10],tmp2ArrEe[10];		
			
		gAllData.delay 					= 20;
		gAllData.batteryAlarm 	= 110;
		gAllData.weldCount 			= gAllData.weldCount;
		gAllData.pulseDelay 		= 5;
		gAllData.shortPulse			= 12;
		gAllData.autoPulse			= 1;
			
		memcpy(tmp2ArrEe, &gAllData,8);
		eeprom_write_bytes(0,tmp2ArrEe,8);
		Serial.println("EEPROM reset");
		
		while(!encBtnState());
	}
}

void sendPulse(){
	//Serial.println("pulse activated");
	unsigned long shortPulseDelay = PulseDelay*ShortPulse/100;
	
	if(shortPulseDelay < 1) shortPulseDelay = 1; 	// so that the delay less than 1 millisecond will round off to 1ms.
	
	digitalWrite(PinPulse,HIGH);
	delay(shortPulseDelay);
	digitalWrite(PinPulse,LOW);
	delay(shortPulseDelay);
	
	digitalWrite(PinPulse,HIGH);
	delay(PulseDelay);
	digitalWrite(PinPulse,LOW);
  WeldCount++;
	lastActiveTime = millis();
}

void updateEeprom(){
	byte tmpArraEe[10],tmp2ArrEe[10];
	if( gAllData.delay != Delay || \
			gAllData.batteryAlarm != BatteryAlarm || \
			gAllData.weldCount != WeldCount || \
			gAllData.pulseDelay != PulseDelay ||\
			gAllData.shortPulse	!= ShortPulse || \
			gAllData.autoPulse	!= AutoPulse ){
		
		gAllData.delay 					= Delay;
		gAllData.batteryAlarm 	= BatteryAlarm;
		gAllData.weldCount 			= WeldCount;
		gAllData.pulseDelay 		= PulseDelay;
		gAllData.shortPulse			= ShortPulse;
		gAllData.autoPulse			= AutoPulse;
		
		memcpy(tmp2ArrEe, &gAllData,8);
		eeprom_write_bytes(0,tmp2ArrEe,8);
		//Serial.println("Updated eeprom");	
	}
}

void CheckBatteryVoltage(){
	static uint8_t LastState = MAIN_SCREEN; 
	uint16_t tmp = analogRead(PinBatVol);
	double tmp1 = tmp * 5 * 4.03 * 10 / 1023 + 6;
	uint8_t tmp2 = (uint8_t)tmp1;
   if (millis() - previousMillis > interval) {
    previousMillis = millis();   // aktuelle Zeit abspeichern
    BatteryVoltage = tmp2; 
   }
	
	
	if(BatteryAlarm > BatteryVoltage && State!=BATTERY_LOW){
		State = BATTERY_LOW;
		LastState = State;
		char tmpAr1[5] = {0,0,0,0,0};
		tmpAr1[0] = BatteryVoltage/100+ '0';	tmpAr1[1] = BatteryVoltage%100/10+ '0';	tmpAr1[2] = '.';	tmpAr1[3] = BatteryVoltage%100%10+ '0';
		lowBatterry(tmpAr1);
	}
	
	if(BatteryAlarm <= BatteryVoltage && State==BATTERY_LOW){
		State = LastState;
	}
}

void CheckForSleep(){
	/*
	if(lastActiveTime + 1000 < millis() ){
		inactiveTime += millis() - lastActiveTime;
		lastActiveTime = millis();
		//Serial.println(inactiveTime);
	
		if(inactiveTime > _STANDBY_TIME_OUT){//(1000*60*_STANDBY_TIME_OUT)){			
			//Serial.println("Enter Standby Mode");
			inactiveTime = 0;
		}
	}		
	*/
	if(lastActiveTime + _STANDBY_TIME_OUT < millis() ){
		if(State!=BATTERY_LOW){
			State = STANDBY;
			standByMsg();
		}
	}	
}

/*-----------------------------------State Machine--------------------------------------*/
void StateMachine(){
	char tmpAr1[5];
	char tmpAr2[5];
	char tmpAr3[5];
	static uint8_t selectedMenu = 0;
	static uint8_t selectedMainMenu = 0;
	static uint8_t selectedSubMenu = 0;
	
	switch(State){
		case STANDBY:
				if( encBtnState()==LOW ){
					State = MAIN_SCREEN;
					delay(30);
					//set all the functionalities anable;
					while(!encBtnState());
				}
			break;
			
		case BATTERY_LOW:
			
		break;
		
		case MAIN_SCREEN:
			State = MAIN_SCREEN_CNT;
			selectedMenu = 0;
			memset(tmpAr1,0,5);
			memset(tmpAr2,0,5);
			memset(tmpAr3,0,5);
			
			tmpAr1[0] = BatteryVoltage/100+ '0';	tmpAr1[1] = BatteryVoltage%100/10+ '0';	tmpAr1[2] = '.';												tmpAr1[3] = BatteryVoltage%100%10+ '0';
			tmpAr2[0] = WeldCount/1000+ '0';			tmpAr2[1] = WeldCount%1000/100+ '0';		tmpAr2[2] = WeldCount%1000%100/10+ '0';	tmpAr2[3] = WeldCount%1000%100%10+ '0';
			tmpAr3[0] = PulseDelay/1000+ '0';			tmpAr3[1] = PulseDelay%1000/100+ '0';		tmpAr3[2] = PulseDelay%1000%100/10+ '0';	tmpAr3[3] = PulseDelay%1000%100%10+ '0';
			
			mainScreen(tmpAr3,tmpAr1,tmpAr2);
			
			break;
		
		case MAIN_SCREEN_CNT:
			if( encBtnState()==LOW ){
				State = MENU_SCREEN;	
				selectedMenu = 0;			
				displayMainMenu(0);
				delay(30);
				//set all the functionalities anable;
				while(!encBtnState());
				break;
			}
			
			if( lastVirtualPosition != VirtualPosition ){			
				if( lastVirtualPosition > VirtualPosition ){
					PulseDelay--;					
				}
				else{		
					PulseDelay++;
				}
				if( PulseDelay <= 1 ) PulseDelay = 1;	
				else if( PulseDelay >= 999)	PulseDelay = 999;	
				
				//PulseDelay = selectedMenu;
				lastVirtualPosition = VirtualPosition;					
			}								
				
			if(lastBatterVoltage!=BatteryVoltage || lastWeldCount != WeldCount || lastPulseDelay != PulseDelay){
				memset(tmpAr1,0,5);
				memset(tmpAr2,0,5);
				memset(tmpAr3,0,5);
				
				tmpAr1[0] = BatteryVoltage/100+ '0';	tmpAr1[1] = BatteryVoltage%100/10+ '0';	tmpAr1[2] = '.';												tmpAr1[3] = BatteryVoltage%100%10+ '0';
				tmpAr2[0] = WeldCount/1000+ '0';			tmpAr2[1] = WeldCount%1000/100+ '0';		tmpAr2[2] = WeldCount%1000%100/10+ '0';	tmpAr2[3] = WeldCount%1000%100%10+ '0';
				tmpAr3[0] = PulseDelay/1000+ '0';			tmpAr3[1] = PulseDelay%1000/100+ '0';		tmpAr3[2] = PulseDelay%1000%100/10+ '0';	tmpAr3[3] = PulseDelay%1000%100%10+ '0';
				
				mainScreen(tmpAr3,tmpAr1,tmpAr2);
				
				lastBatterVoltage=BatteryVoltage;
				lastWeldCount = WeldCount;
				lastPulseDelay = PulseDelay;
				
			}
			
			//other functions
			break;
		
		case MENU_SCREEN:		
			if( encBtnState()==LOW ){
				delay(30);
				State = SUB_MENU_1;
				selectedMainMenu = selectedMenu;
				if(selectedMainMenu == 0){
					displaySubMenuType1(selectedMenu);
				}
				else if(selectedMainMenu == 1){
					uint8_t value = BatteryAlarm;		
					memset(tmpAr1,0,5);				
					tmpAr1[0] = value/100+'0';
					tmpAr1[1] = value%100/10+'0';
					tmpAr1[2] = '.';
					tmpAr1[3] = value%100%10+'0';
					displaySubMenuType2("Battery Alarm: ", tmpAr1 , "voltage");
				}
				else if(selectedMainMenu == 2){
					uint8_t value = ShortPulse;
					memset(tmpAr1,0,5);	
					tmpAr1[0] = value/100+'0';
					tmpAr1[1] = value%100/10+'0';
					tmpAr1[2] = value%100%10+'0';
					displaySubMenuType2("Short Pulse: ", tmpAr1 , "% of pulse time");		
				}
				selectedMenu = 0;
				//set all the functionalities anable;
				while(!encBtnState());	
				break;
			}
			
			if( lastVirtualPosition != VirtualPosition ){		
				if( lastVirtualPosition > VirtualPosition ){
					selectedMenu--;
				}
				else{		
					selectedMenu++;
				}
				if( selectedMenu >= 250){
					selectedMenu = 0;
				}
				else if( selectedMenu >= 2){
					selectedMenu = 2;
				}
				
				lastVirtualPosition = VirtualPosition;
				displayMainMenu(selectedMenu);
			}		
			break;
		
		case SUB_MENU_1:
			if( encBtnState()==LOW ){
				delay(30);
				//set all the functionalities anable;
				if(selectedMainMenu==0){
					State = SUB_MENU_2;
					selectedSubMenu = selectedMenu;
					
					if(selectedSubMenu==0){
						if(AutoPulse == 0){
							displaySubMenuType2("Auto Pulse: On/Off", "ON" , " ");
							AutoPulse = 1;
						}
						else if(AutoPulse == 1){
							displaySubMenuType2("Auto Pulse: On/Off", "OFF" , " ");
							AutoPulse = 0;
						}
					}
					else if(selectedSubMenu==1){
						uint8_t value = Delay;
						memset(tmpAr1,0,5);				
						tmpAr1[0] = value/10+'0';
						tmpAr1[1] = '.';
						tmpAr1[2] = value%10+'0';
						displaySubMenuType2("Auto Pulse: Delay", tmpAr1 , "seconds");
					}
					else{
					
					}
					selectedMenu = 0;
				}
				else if(selectedMainMenu == 1){					
					State = MAIN_SCREEN;
					selectedMenu = 0; 
				}
				else if(selectedMainMenu == 2){					
					State = MAIN_SCREEN;
					selectedMenu = 0;
				}
				else{			
					State = MAIN_SCREEN;
					selectedMenu = 0;
				}
				while(!encBtnState());	
				selectedMenu = 0;
				break;
			}
			
			if(selectedMainMenu==0){
				if( lastVirtualPosition != VirtualPosition ){		
					if( lastVirtualPosition > VirtualPosition ){
						selectedMenu--;
					}
					else{		
						selectedMenu++;
					}
					
					if( selectedMenu >= 3){
						selectedMenu = 2;
					}
					
					lastVirtualPosition = VirtualPosition;
					displaySubMenuType1(selectedMenu);
				}					
			}
			else if(selectedMainMenu == 1){
				
				if( lastVirtualPosition != VirtualPosition ){						
					
					if( lastVirtualPosition > VirtualPosition ){
						BatteryAlarm--;
						
					}
					else{		
						BatteryAlarm++;
					}
					if( BatteryAlarm <= 100 ) BatteryAlarm = 100;	
					else if( BatteryAlarm >= 200)	BatteryAlarm = 200;					
					
					lastVirtualPosition = VirtualPosition;	
					
					uint8_t value = BatteryAlarm;			
					memset(tmpAr1,0,5);				
					tmpAr1[0] = value/100+'0';
					tmpAr1[1] = value%100/10+'0';
					tmpAr1[2] = '.';
					tmpAr1[3] = value%100%10+'0';
					displaySubMenuType2("Battery Alarm: ", tmpAr1 , "voltage");				
				}								
			}
			else if(selectedMainMenu == 2){
				if( lastVirtualPosition != VirtualPosition ){					
					
					if( lastVirtualPosition > VirtualPosition ){
						ShortPulse--;
					}
					else{		
						ShortPulse++;
					}
					if( ShortPulse <= 1 ) ShortPulse = 1;
					else if( ShortPulse >= 100)	ShortPulse = 100;									
					
					lastVirtualPosition = VirtualPosition;	
					uint8_t value = ShortPulse;
					memset(tmpAr1,0,5);	
					tmpAr1[0] = value/100+'0';
					tmpAr1[1] = value%100/10+'0';
					tmpAr1[2] = value%100%10+'0';
					displaySubMenuType2("Short Pulse: ", tmpAr1 , "% of pulse time");					
				}								
			}
			else{
			}
			
			break;
			
		case SUB_MENU_2:			
			if( encBtnState()==LOW ){
				delay(30);
				//set all the functionalities anable;
				State = MAIN_SCREEN;
				while(!encBtnState());	
				selectedMenu = 0;
				break;
			}
			
			if(selectedSubMenu==0){
				if( lastVirtualPosition != VirtualPosition ){
					
					
					if( lastVirtualPosition > VirtualPosition ){
						AutoPulse--;
					}
					else{		
						AutoPulse++;
					}
					if( AutoPulse <= 0 ) AutoPulse = 0;
					else if( AutoPulse >= 1)	AutoPulse = 1;

					
					lastVirtualPosition = VirtualPosition;
					if(AutoPulse == 0){
						displaySubMenuType2("Auto Pulse: On/Off", "ON" , " ");
					}
					else if(AutoPulse == 1){
						displaySubMenuType2("Auto Pulse: On/Off", "OFF" , " ");
					}	
				}
			}
			else if(selectedSubMenu==1){
				if( lastVirtualPosition != VirtualPosition ){					
					
					if( lastVirtualPosition > VirtualPosition ){
						Delay--;
					}
					else{		
						Delay++;
					}
					if( Delay >= 50)	Delay = 50;
					else if( Delay <= 5 ) Delay = 5;

					
					lastVirtualPosition = VirtualPosition;
					
					uint8_t value = Delay;
					memset(tmpAr1,0,5);				
					tmpAr1[0] = value/10+'0';
					tmpAr1[1] = '.';
					tmpAr1[2] = value%10+'0';
					displaySubMenuType2("Auto Pulse: Delay", tmpAr1 , "seconds");
				}
			}
			else{
			
			}	
			
			break;
			
		default:
			break;
	}
}

bool encBtnState(){	
	if(!digitalRead(PinSW)){
		lastActiveTime = millis();
	}
	return (digitalRead(PinSW));
}


/*--------------------------------------- isr ------------------------------------------*/
void isr(){                    
	unsigned long interruptTime = millis();
	if (interruptTime - lastInterruptTime > 20){
	/*
		if (digitalRead(PinCLK)){
			if(digitalRead(PinDT)){			
			}
			else{
				VirtualPosition++;		
			}
		}
		else{
			if(digitalRead(PinDT)){
				VirtualPosition--;
			}
		} 
		*/
		if(digitalRead(PinDT)){
			VirtualPosition--;
		}
		else{
			VirtualPosition++;		
		}
		lastInterruptTime = interruptTime;
		lastActiveTime = interruptTime;
	}
}

/*--------------------------------- Display Functions ----------------------------------*/
void displayMainMenu(uint8_t SelectedItem){
	uint8_t _GAP = 4;
  display.clearDisplay();
  display.setCursor(1,_GAP);
	display.setTextSize(2);
	
  display.setTextColor(WHITE);
  if(SelectedItem == 0) display.setTextColor(BLACK, WHITE);
  display.println("Auto Pulse");
	
  display.setCursor(1,(2*_GAP+16));
  display.setTextColor(WHITE);
  if(SelectedItem == 1) display.setTextColor(BLACK, WHITE);
  display.println("Btry Alarm");
	
  display.setCursor(1,(3*_GAP + 2*16));
  display.setTextColor(WHITE);
  if(SelectedItem == 2) display.setTextColor(BLACK, WHITE);
  display.println("Shrt Pulse");
	
  display.display();	
}

void displaySubMenuType1( uint8_t SelectedItem ){
	uint8_t _GAP = 4;
  display.clearDisplay();
	
  display.setCursor(1,_GAP);
	display.setTextSize(1);	
  display.setTextColor(WHITE);
  display.println("Auto Pulse:");
	
	display.setTextSize(2);	
  display.setCursor(1,(2*_GAP+16 - 8));
  display.setTextColor(WHITE);
  if(SelectedItem == 0) display.setTextColor(BLACK, WHITE);
  display.println("ON/OFF");
	
	display.setTextSize(2);	
  display.setCursor(1,(3*_GAP + 2*16 - 8));
  display.setTextColor(WHITE);
  if(SelectedItem == 1) display.setTextColor(BLACK, WHITE);
  display.println("Delay");
	
	display.setTextSize(1);		
  display.setCursor(1,(4*_GAP + 3*16 - 8));
  display.setTextColor(WHITE);
  if(SelectedItem == 2) display.setTextColor(BLACK, WHITE);
  display.println("Exit");
	
  display.display();	
}

void displaySubMenuType2( const char * menuName, const char *value, const char * units){
	uint8_t _GAP = 4;
  display.clearDisplay();
	
  display.setCursor(1,_GAP);
	display.setTextSize(1);	
  display.setTextColor(WHITE);
  display.println(menuName);
	
	display.setTextSize(2);	
  display.setCursor(1,(3*_GAP + 16 - 8));
  display.setTextColor(WHITE);
  display.println(value);
	
	display.setTextSize(1);	
  display.setCursor(1,(4*_GAP + 2*16 - 8));
  display.setTextColor(WHITE);
  display.println(units);	
	
  display.display();	
}

void mainScreen( const char * pulseTime, const char * batteryV, const char * totalWelds){
	uint8_t _GAP = 5;
  display.clearDisplay();
	
  display.setCursor(1,_GAP);
	display.setTextSize(2);	
  display.setTextColor(WHITE);
  display.print("  ");
  display.print(pulseTime);
  display.println(" ms");
	
	display.setTextSize(1);	
  display.setCursor(1,(3*_GAP + 16));
  display.setTextColor(WHITE);
  display.println("Battery:");
	
	display.setTextSize(1);	
  display.setCursor(64,(3*_GAP + 16));
  display.setTextColor(WHITE);
  display.println("Tot Welds:");
	
	display.setTextSize(1);	
  display.setCursor(1,(4*_GAP + 2*16 - 8));
  display.setTextColor(WHITE);
  display.println(batteryV);
	
	display.setTextSize(1);	
  display.setCursor(64,(4*_GAP + 2*16 - 8));
  display.setTextColor(WHITE);
  display.println(totalWelds);	
	
	display.setTextSize(1);	
  display.setCursor(96,(5*_GAP + 1*16 + 2*8));
  display.setTextColor(WHITE);
  if(AutoPulse==0) display.print("AUTO");
	else display.print("MANU");
  display.display();	
}

void lowBatterry( const char * batteryV ){
	uint8_t _GAP = 2;
  display.clearDisplay();
	
  display.setCursor(1,_GAP);
	display.setTextSize(2);	
  display.setTextColor(WHITE);
  display.println("   LOW   ");
	
  display.setCursor(1,(2*_GAP + 16));
  display.println(" BATTERY ");
	
	display.setTextSize(2);	
  display.setCursor(1,(3*_GAP + 2*16));
  display.print("  ");
  display.print(batteryV);		
  display.println("V");	
	
  display.display();	
}
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

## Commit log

2017-09-01 Create Arduino PCB
2017-09-08 added little bit bigger tolerances
    [ANL_Fuse_Case_Top.stl]
